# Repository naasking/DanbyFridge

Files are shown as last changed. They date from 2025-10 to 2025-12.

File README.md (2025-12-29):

# Danby Fridge Microcontroller Project

I upcycled an old Danby Fridge, replacing the broken thermostat with an ESP32-C3,
a thermistor for temperature monitoring, and a relay to control the compressor.

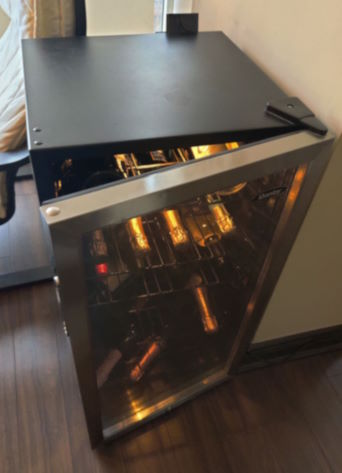
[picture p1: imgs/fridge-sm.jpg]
Danby Fridge
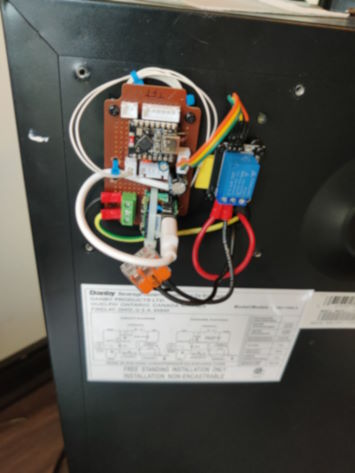
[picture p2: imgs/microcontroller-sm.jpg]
Microcontroller
 

This was also an experiment in AI programming, as the initial skeleton and various
refinements were managed using VS Code + Cline and the gpt-5-mini model, along with
some reviews using Copilot GPT-5.

# User Interface

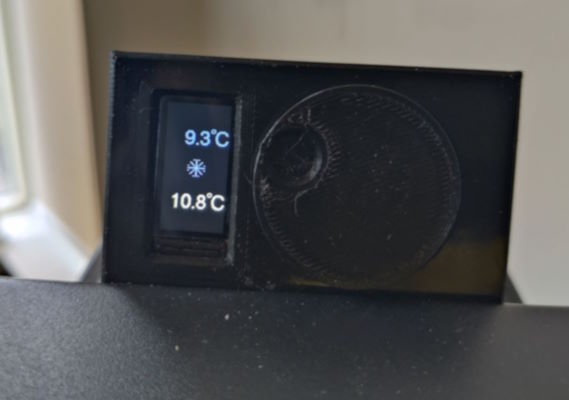
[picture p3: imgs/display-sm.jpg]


Use the dial to set the target temperature, shown in blue at the top. The temperature
at the bottom is the current reading from the thermistor. Press and hold the dial
to switch between Fahrenheit and Celsius.

The snowflake will render when the compressor is actively running, although you can
typically hear it anyway.

# Features

 * Switching between Celsius and Fahrenheit
 * Hysterisis around target temperature
 * Compressor minimum off time to increase longevity of the PTC starter
 * Ratiometric averaging of ADC readings to factor out supply voltage fluctiations
 * Moving averages and dead times to handle ESP32 ADC inaccuracies
 * Periodic state saving only when changes occurred to save on writes

# Design Notes and the AI experience

Using AI for programming can be simultaneously frustrating and humbling. It does a reasonably
good job at following instructions and the code quality is decent, but sometimes we can fall
into rabbit holes without end.

Getting the RMT code working turned out to be futile, but it was never clear whether this was
an issue with the code or the sensor, so I eventually abandoned it for a simple thermistor. I
later discovered a library that does the RMT so maybe I'll try that some day.

There were a few humblind situations where the AI told me of specific issues with
a piece of code, and I thought I had ruled them out, but I'm sometimes not as clever and thorough
as I think.

The `async.h` and `rotary.h` are reusable, standalone headers from my [embedded](https://github.com/naasking/embedded)
repository. They simplified the code a lot, and I was able to easily tell GPT-5 to rewrite
some of the code using these headers. It also suggested a few refinements to the headers
which then made it upstream. Neat.

# Microcontroller Circuit

This is a rough schematic of the controller portion:

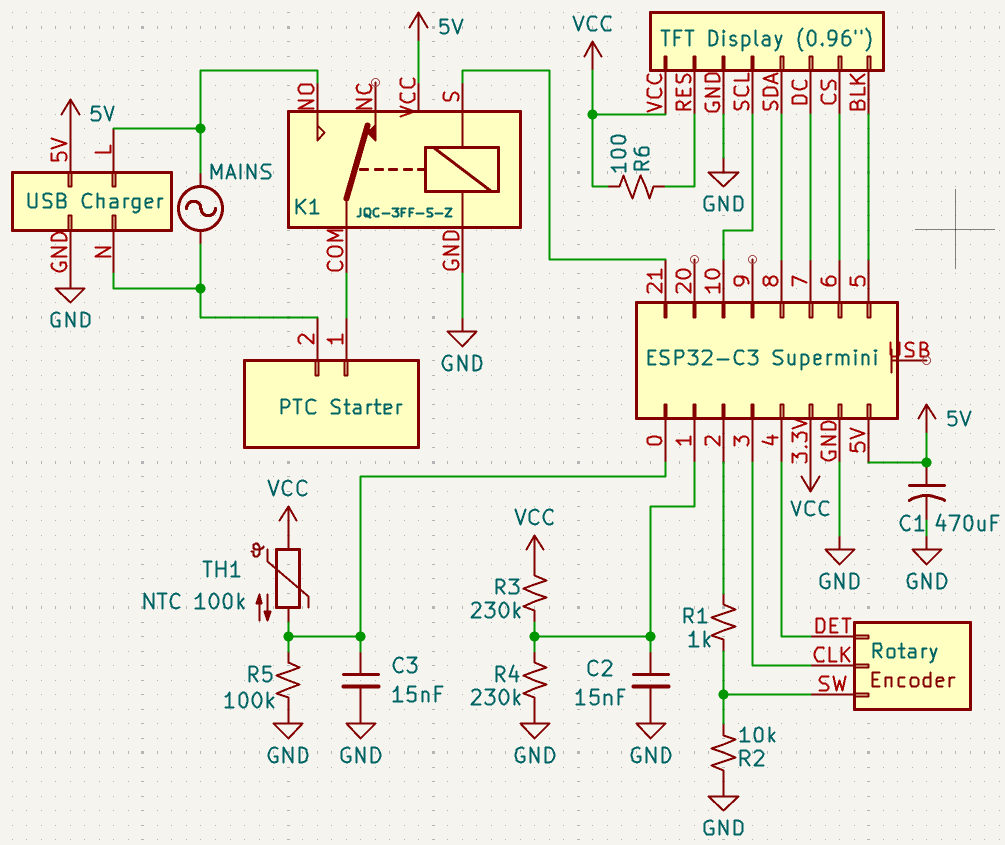
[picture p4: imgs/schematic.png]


It's just missing the small snubber circuit across the relay's AC pins.

# Future Work

## Microcontroller Sleep

I had started with the intention of putting the microcontroller into low power mode
and only powering it up to take measurements every 5 seconds or so. However, I ran into
many difficulties getting RMT to work with the DHT22 sensor I initially started with,
so I disabled a lot of this functionality to try to narrow down the issues I was having
and never got around to adding this back.

## Refactoring

There are a lot of static variables, which limits how you can reuse this code for
different types of fridges. For instance, dual zone wine fridges require multiple
thermistors and multiple relays, which isn't easy with the current code.

All of the static variables should be refactored into structs and initialized in
static arrays whose sizes are set by compile-time constants. This would let the
code scale.

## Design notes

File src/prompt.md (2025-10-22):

Write an Arduino program with the following requirements:

1. It periodically takes temperature readings from a DHT22 sensor.
2. Let's a user modify the target temperature via a HW-040 rotary encoder whose rotation is tracked by an interrupt service routine.
3. Each click of the rotary encoder should correspond to 0.1 degrees C.
4. It displays the current temperature and target temperatures on an ST7735 display, 160x80 resolution.
5. Checks the target and current temperature periodically, and activates a relay when they differ until the current temperature matches the target.
6. It goes into low power mode if no user activity detected for some time.
7. All operations should be non-blocking so the display and rotary encoder counting is responsive.

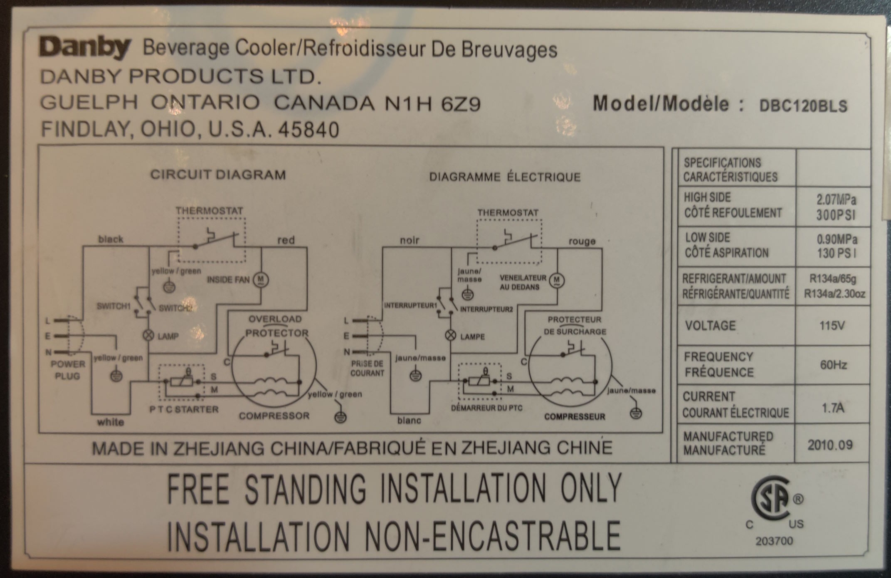
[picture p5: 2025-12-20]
imgs/original circuit.jpg

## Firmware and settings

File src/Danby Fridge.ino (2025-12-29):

#include <Adafruit_ST7735.h>
#include <Fonts/FreeSans12pt7b.h>
#include <SPI.h>                 // ESP32 core SPI
#include <Preferences.h>         // for saving data
#include "rotary.h"
#include <esp_sleep.h>
#include <esp_pm.h>
#include "async.h"

// Preferences instance for non-volatile storage on ESP32
static Preferences prefs;

// === ESP32-C3 Super mini Pin Mapping ===
#define THERM_PIN       0  // Safe -- connected to thermistor
#define RELAY_PIN       21 // Safe -- connected to KY-019 relay module
#define VREF_PIN        1  // Safe -- connected to voltage reference to correct for voltage dips

// Rotary encoder -- grouped on the right side
#define ROTARY_SW       2  // Strapping: should default high
#define ROTARY_CLK      3  // Safe
#define ROTARY_DT       4  // Safe

// TFT SPI -- grouped on the left side
#define TFT_DC          7   // Safe
#define BACKLIGHT_PIN   5   // Safe
#define TFT_CS          6   // Safe
#define TFT_MOSI        8   // SDA-Strapping if GPIO2 is low
#define TFT_SCK         10  // SCL-Safe
#define TFT_MISO       -1   // Not used

// === Notes ===
// - All pins are 3.3V only (no 5V tolerance).

// ADC config
// measured 2.4V on a 3.3V rail as the reference
#define VREF_K          2.41f/3.3f
#define SAMPLES_TOTAL   64
#define SAMPLE_DELAY_MS 10

// Thermistor constants -- use a 100K NTC 3950
// #define R_FIXED 94200.0f    // ~100kΩ reference resistor
// #define R0      125000.0f   // 100kΩ at 25 °C
#define R_FIXED 100000.0f    // ~100kΩ reference resistor
#define R0      100000.0f   // 100kΩ at 25 °C
#define BETA    3950.0f
#define T0      298.15f     // 25 °C in Kelvin

// EMA smoothing factor
#define EMA_ALPHA 0.1f   // adjust between 0.05–0.2 depending on smoothness

#define DISPLAY_UPDATE_INTERVAL 200
#define CONTROL_INTERVAL 10000
#define HYSTERESIS_TENTHS 5      // 0.5°C hysteresis
#define ENCODER_STEP_TENTHS 1    // 0.1°C per encoder step
#define ENCODER_PULSES_PER_STEP 2 // quadrature pulses per mechanical detent (tune if needed)
#define BUTTON_DEBOUNCE_MS 50
#define LONG_PRESS_MS 1000 // ms for long press to toggle units

/* Persistence (Preferences) */
#define SAVE_INTERVAL_MS 5000    // minimum interval between non-volatile writes

// Power management
#define WDT_SLEEP_S 8            // WDT sleep interval in seconds (LowPower SLEEP_8S)
#define CONTROL_INTERVAL_S 10    // control interval in seconds (approximately)
#define DISPLAY_ON_AFTER_WAKE_MS 10000 // keep display on for some time after wake for user feedback
#define COMPRESSOR_MIN_OFF_MS (4UL * 60UL * 1000UL) // 4 minutes minimum off time for compressor starter
#define THERM_START_DELAY 10000

#define _println(text)
#define _printf(fmt, arg0)
//#define _println(text) if (Serial && Serial.isConnected()) Serial._println(text)
//#define _printf(fmt, arg0) if (Serial && Serial.isConnected()) Serial.printf(fmt, arg0)

// RST tied HIGH on module; pass -1 to disable software reset
Adafruit_ST7735 tft = Adafruit_ST7735(TFT_CS, TFT_DC, -1);

// Thermistor async function state
typedef struct {
    async_state;                // the async state
    int sampleCount;            // the number of samples taken
    uint32_t temp;              // accumulated temperature reading
    unsigned long lastSampleMs; // last time a sample was taken
    bool expMovingAvg;          // smoothing is enabled
    float vRef;                 // voltage divider reference
} ThermistorState;

ThermistorState thermState;

// Internal state stored in tenths of °C to avoid non-atomic float access
volatile int16_t targetTenthsC = 250; // tenths of a degree C = 25.0°C

// Quadrature decoder state (4-bit history) and pulse accumulator.
// ISR calls rotary_step() and increments encoderPulseCount.
volatile uint8_t rot_state = 0;
volatile int16_t encoderPulseCount = 0;
 
// Persistence helpers
unsigned long lastSaveMs = 0;

// Compressor/relay safety
bool relayOn = false;
unsigned long lastRelayOffMs = 0;

bool displayCelsius = true;
unsigned long displayOnMs = 0;
unsigned long wdtWakeCount = 0;
float lastValidTempC = NAN;
bool lastButtonState = HIGH;
unsigned long lastButtonMs = 0;
unsigned long pressStartMs = 0;

/// @brief Flag indicating that the target temperature has changed.
/// @remarks Must be a global because changes could happen before the last save window elapses
bool targetDirty = false;
bool unitsDirty = false; // true when the units selection needs persisting

// fixed width text bounds
uint16_t textWidth, textHeight;

void IRAM_ATTR encoderISR() {
  // Minimal ISR: use rotary_step_s16 to update encoderPulseCount directly.
  // rotary_step_s16 expects (count, state, rotb, rota).
  // Read DT (rotb) first, then CLK (rota), and pass in that order to avoid swapped inputs.
  uint8_t a = digitalRead(ROTARY_DT);  // rota (LSB)
  uint8_t b = digitalRead(ROTARY_CLK); // rotb (MSB)
  rotary_step_s16(&encoderPulseCount, &rot_state, b, a);
}

// Wake-only ISR for the rotary button: intentionally empty so its only effect
// is to wake the MCU from sleep. Debounce and button handling remain in loop().
void IRAM_ATTR wakeISR() {
  // no-op: wake-only
}

void setup() {
  // set this LOW immediately so the compressor doesn't immediately turn on
  pinMode(RELAY_PIN, OUTPUT);
  digitalWrite(RELAY_PIN, LOW);

  //Serial.begin(115200, SERIAL_8N1, -1);
  Serial.begin(115200);
  Serial.setTxTimeoutMs(0);
  //delay(3000);
  _println("Program started...");

  // Initialize SPI with explicit pins for ESP32-C3
  SPI.begin(TFT_SCK, TFT_MISO, TFT_MOSI, TFT_CS);

  // Ensure control pins are configured and stable before calling library init.
  pinMode(TFT_CS, OUTPUT);
  pinMode(TFT_DC, OUTPUT);

  // Initialize SPI with a slower clock speed so it's more stable, otherwise
  // the scren sometimes blanks out when receiving many rotary pulses.
  SPI.beginTransaction(SPISettings(4000000, MSBFIRST, SPI_MODE0));
  digitalWrite(TFT_CS, HIGH);
  digitalWrite(TFT_DC, HIGH);
  SPI.endTransaction();

  delay(10); // allow peripheral to settle

  // Call library init (use MINI160x80 PLUGIN for this module)
  tft.initR(INITR_MINI160x80_PLUGIN);
  tft.setFont(&FreeSans12pt7b);
  {
    int16_t x, y;
    char text[] = "-CC.CCC";
    tft.getTextBounds(text, 0, 100, &x, &y, &textWidth, &textHeight);
  }
  tft.setTextSize(1);
  tft.setRotation(0);
  tft.enableDisplay(true);
  tft.fillScreen(ST7735_BLACK);

  pinMode(THERM_PIN, INPUT);
  pinMode(VREF_PIN, INPUT);
  pinMode(ROTARY_CLK, INPUT_PULLUP);
  pinMode(ROTARY_DT, INPUT_PULLUP);
  pinMode(ROTARY_SW, INPUT_PULLUP);

  // Backlight control pin (module BLK has onboard transistor)
  pinMode(BACKLIGHT_PIN, OUTPUT);
  digitalWrite(BACKLIGHT_PIN, HIGH);

  unsigned long now = millis();
  displayOnMs = now + DISPLAY_ON_AFTER_WAKE_MS;

  attachInterrupt(digitalPinToInterrupt(ROTARY_CLK), encoderISR, CHANGE);
  // Also attach to DT so the ISR runs on changes of either channel (better capture on fast/cheap encoders)
  attachInterrupt(digitalPinToInterrupt(ROTARY_DT), encoderISR, CHANGE);
  // Wake-only interrupt for rotary pushbutton (FALLING edge). ISR does nothing
  // beyond waking the MCU; actual button processing is done in the loop.
  attachInterrupt(digitalPinToInterrupt(ROTARY_SW), wakeISR, FALLING);

  // initialize relay OFF (assumes active HIGH; invert logic if needed)
  //FIXME: should maybe check if relay is already on and needs to be?
  digitalWrite(RELAY_PIN, LOW);

  // Load persisted target temperature (tenths of °C). Validate range, otherwise set to current measured temp if available.
  prefs.begin("fridge", false);

  // Try to load saved target
  int16_t saved = prefs.getShort("targetC", INT16_MIN);
  targetTenthsC = saved >= -400 && saved <= 500
    ? saved
    : 250;  // default 25.0C

  // Load persisted units selection (true = Celsius). Default to Celsius if missing.
  displayCelsius = prefs.getBool("unitsC", true);

  // keep Preferences open for the lifetime of the program (do not end here)
  // prefs.end(); // removed to keep prefs active

  // initialize save timestamp to avoid immediate write
  lastSaveMs = now;

  // initialize the thermistor task
  async_init(&thermState);
  thermState.expMovingAvg = false;

  // let system settle for THERM_START_DELAY before reading
  thermState.lastSampleMs = now + THERM_START_DELAY;

  // ensure display shows current values at startup
  updateDisplay(lastValidTempC, targetTenthsC);
}

void show(float temp, int16_t x, int16_t y, uint16_t color) {
  // bounds calculation is slightly off
  tft.setTextColor(color);
  tft.fillRect(x, y - textHeight, textWidth + 20, textHeight + 1, ST77XX_BLACK);
  if (isnan(temp)) {
    // error code should print out 7 chars to match expected length
    tft.setCursor(x, y);
    tft.printf(" - - - - - ");
  } else {
    char buf[16];
    char symbol = displayCelsius ? 'C' : 'F';
    if (!displayCelsius) {
      temp = temp * 9.0 / 5.0 + 32.0;
    }
    // numeric field: width 5 (space/sign + up to 2 digits + '.' + 1 decimal) + " C" = 7 chars
    snprintf(buf, sizeof(buf), "%5.1f %c", temp, symbol);
    // right-align the text
    int16_t x1, y1;
    uint16_t w, h;
    tft.getTextBounds(buf, x, y, &x1, &y1, &w, &h);
    tft.setCursor(78 - w, y);
    tft.print(buf);
    tft.drawCircle(x + textWidth - 4, y - textHeight / 2 + 6, 2, color);
  }
}

void updateDisplay(float currentC, int16_t targetTenths) {
  // Full-screen redraw but use color to distinguish current (white) and target (light blue).
  //_println("updating display...");

  // Target temperature (right) in light blue - also fixed-width
  uint16_t lightBlue = tft.color565(120, 120, 255); // light blue (RGB: 120,120,255)
  float tgtC = targetTenths / 10.0;
  show(tgtC, 0, 50, lightBlue);

  // Current temperature (left) - print fixed-width numeric + unit to avoid residual chars
  show(currentC, 0, 130, ST77XX_WHITE);

  // Compressor running indicator (snowflake) between the values
  // Draw a simple snowflake icon centered at (40, 80)
  int cx = 40, cy = 80, size = 10;
  //tft.fillRect(0, cy - size - 1, 80, size + 1, ST77XX_RED);
  tft.fillRect(0, cy - size, 80, 2*size, ST77XX_BLACK);
  if (relayOn) {
    uint16_t color = lightBlue;
    tft.drawPixel(cx, cy, color);

    // main arms (horizontal & vertical)
    tft.drawLine(cx - size, cy, cx + size, cy, color); // horizontal
    tft.drawLine(cx, cy - size, cx, cy + size, color); // vertical

    // diagonals (scaled to ~70% of size for aesthetics)
    int diag = size * 0.7;
    tft.drawLine(cx - diag, cy - diag, cx + diag, cy + diag, color);
    tft.drawLine(cx - diag, cy + diag, cx + diag, cy - diag, color);

    // small branches: one pixel offset perpendicular to each arm end
    // Horizontal arms
    int bsize = size / 3;
    tft.drawPixel(cx - size, cy - bsize, color);
    tft.drawPixel(cx - size, cy + bsize, color);
    tft.drawPixel(cx + size, cy - bsize, color);
    tft.drawPixel(cx + size, cy + bsize, color);

    // Vertical arms
    tft.drawPixel(cx - bsize, cy - size, color);
    tft.drawPixel(cx + bsize, cy - size, color);
    tft.drawPixel(cx - bsize, cy + size, color);
    tft.drawPixel(cx + bsize, cy + size, color);
  } else {
    // If compressor off, optionally draw a faint outline or nothing. We'll draw nothing.
  }
}

/// @brief  Read the thermistor value.
/// @param s    The thermistor state.
/// @param now  The current time, bound to mills().
/// @return     The async function status.
async readThermistor(ThermistorState *s, unsigned long now, float* temp) {
    async_begin(s);

    s->sampleCount = 0;
    s->temp = 0;
    s->vRef = 0;

    while (s->sampleCount < SAMPLES_TOTAL) {
        // wait between samples for SAMPLE_DELAY_MS
        // also wait at boot for THERM_START_DELAY to start taking measurements
        // to let the system settle
        await(now - s->lastSampleMs < THERM_START_DELAY
           && now - s->lastSampleMs >= SAMPLE_DELAY_MS);
        s->lastSampleMs = now;

        // Read thermistor node
        (void)analogRead(THERM_PIN);   // throw-away after mux switch
        delayMicroseconds(300);
        s->temp += analogRead(THERM_PIN);
        
        // Read 3.3V sense node
        (void)analogRead(VREF_PIN);    // throw-away after mux switch
        delayMicroseconds(300);
        s->vRef += analogRead(VREF_PIN);
        s->sampleCount++;
    }

    // Compute ratiometric average ADC value using a voltage reference on another ADC pin
    {
      float vTemp = (float)s->temp / SAMPLES_TOTAL;
      float vRef = (float)s->vRef / SAMPLES_TOTAL;

      // Compute thermistor resistance
      float rTherm = R_FIXED * (vRef / (vTemp * VREF_K) - 1.0f);

      // Beta equation
      float invT = (1.0f / T0) + (1.0f / BETA) * logf(rTherm / R0);
      float tempK = 1.0f / invT;
      float tempC = tempK - 273.15f - 1.0f; // +1.0C bias as measured by ice slurry
      _printf("Temp: %f", tempC);
      if (s->expMovingAvg) {
        *temp = EMA_ALPHA * tempC  + (1.0f - EMA_ALPHA) * *temp;
      } else {
        s->expMovingAvg = true;
        *temp = tempC;
      }
    }
    async_end;
}

/// @brief Relay control function
/// @returns True if the comrpessor has changed state, false otherwise.
bool controlTemperature(unsigned long now, float currentC, int16_t targetTenths) {
  // Skip if the reading is invalid or if the relay is off and it was on is before the min cool-off
  if (isnan(currentC) || !relayOn && (now - lastRelayOffMs) < COMPRESSOR_MIN_OFF_MS)
    return false;

  int16_t currentTenths = (int16_t)round(currentC * 10.0);

  // Need to turn ON when current is above target plus hysteresis.
  if (!relayOn && currentTenths >= (targetTenths + HYSTERESIS_TENTHS)) {
    // Only allow starting compressor if it is currently off and the minimum off time has elapsed.
    digitalWrite(RELAY_PIN, HIGH);
    relayOn = true;
    return true;
  } else if (relayOn && currentTenths <= (targetTenths - HYSTERESIS_TENTHS)) {
    // Need to turn OFF when current is below target minus hysteresis.
    digitalWrite(RELAY_PIN, LOW);
    relayOn = false;
    lastRelayOffMs = now;
    return true;
  }
  return false;
}

void loop() {
  bool displayDirty = false;
  unsigned long now = millis();
  int16_t pulses = 0;

  // Consume encoder pulses produced by the quadrature ISR and convert pulses -> steps
  {
    noInterrupts();
    pulses = encoderPulseCount;
    encoderPulseCount = 0;
    interrupts();

    if (pulses != 0) {
      static int16_t remainder = 0;
      remainder += pulses;
      int16_t steps = remainder / ENCODER_PULSES_PER_STEP;
      remainder = remainder % ENCODER_PULSES_PER_STEP;

      if (steps != 0) {
        int16_t newTarget = targetTenthsC + (int16_t)(steps * ENCODER_STEP_TENTHS);
        if (newTarget < -100) newTarget = -100;
        if (newTarget > 500)  newTarget = 500;
        if (newTarget != targetTenthsC) {
          targetTenthsC = newTarget;
          targetDirty = true;
          displayDirty = true;
        }
      }
    }
  }

  // button press to wake board from sleep and turn on screen
  // long-press to switch temperature units
  bool sw = digitalRead(ROTARY_SW);
  if (sw == LOW) {
    if (lastButtonState == HIGH && (now - lastButtonMs) > BUTTON_DEBOUNCE_MS) {
      // Debounced button press
      pressStartMs = now;
      lastButtonMs = now;
      displayDirty = true;
    }
    if ((now - pressStartMs) >= LONG_PRESS_MS) {
      // Long press: toggle units
      displayCelsius = !displayCelsius;
      unitsDirty = true;            // mark units changed so we persist it
      pressStartMs = now; // reset the hold period
      displayDirty = true;
    }
  }
  if (sw == HIGH && lastButtonState == LOW && (now - lastButtonMs) > BUTTON_DEBOUNCE_MS) {
    // Button released
    lastButtonMs = now;
  }
  lastButtonState = sw;
  
  // Keep display on for a short period after any updates for user feedback
  // This MUST be a <= comparison as two subsequent iterations might have the same `now` value.
  // While pulses are being registered, this keeps pushing `displayOnMs` forwards and the subsequent
  // loop iterations pull the pin LOW, eventually pushing it HIGH once no pulses are recorded and
  // `now` advances slightly.  This ends up looking like a PWM signal and the screen noticeably
  // dims as a result.
  bool displayOn = (displayOnMs - now) <= (unsigned long)DISPLAY_ON_AFTER_WAKE_MS;
  digitalWrite(BACKLIGHT_PIN, displayOn ? HIGH : LOW);
  
  //  Put MCU to low-power sleep if idle: wake sources are external INT (encoder/button) and timer (approx WDT)
  //  Only sleep if no recent activity and display not required.
  bool idle = (pulses == 0) && !targetDirty && !displayDirty;
  if (!idle) {
    displayOnMs = now + DISPLAY_ON_AFTER_WAKE_MS;
  } else if (!displayOn) {
    // // Configure timer wake for approximately WDT_SLEEP_S seconds (esp_light_sleep)
    // esp_sleep_enable_timer_wakeup((uint64_t)WDT_SLEEP_S * 1000000ULL);
    // // Enter light sleep; external interrupts attached with attachInterrupt() will also wake the chip
    // esp_light_sleep_start();
    // Woke up (either via timer or external INT)
    // wdtWakeCount++;
    // keep display on briefly after wake for feedback
    // displayOnMs = now + DISPLAY_ON_AFTER_WAKE_MS;
  }

  // measure the current temperature
  float t = lastValidTempC;
  if (readThermistor(&thermState, now, &t) == ASYNC_DONE) {
    displayDirty = isnan(lastValidTempC) || abs(t - lastValidTempC) > 0.1f;
    lastValidTempC = t;
    async_init(&thermState);
  }
  
  // Persist target temperature occasionally (rate-limited to SAVE_INTERVAL_MS)
  if ((targetDirty || unitsDirty) && (now - lastSaveMs >= SAVE_INTERVAL_MS)) {
    // Local copies to avoid races with ISRs/other logic
    int16_t toSave = targetTenthsC;
    bool unitsToSave = displayCelsius;
    _println("Save settings");
    // Preferences is already opened in setup and kept open; just write the values
    prefs.putShort("targetC", toSave);
    prefs.putBool("unitsC", unitsToSave);
    lastSaveMs = now;
    targetDirty = false;   // reset dirty state
    unitsDirty = false;
  }
  
  // Relay control based on temperature -- it should monitor temperature regardless
  // of whether something has changed, it should only depend on the amount of time
  // the relay has been off. Mark the display as dirty if the relay changes state.
  displayDirty |= controlTemperature(now, lastValidTempC, targetTenthsC);

  // Single display update point: update once per loop if any condition requested it.
  if (displayDirty) {
    updateDisplay(lastValidTempC, targetTenthsC);
  }
}

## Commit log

2025-10-15 rewritten to handle multiple timing and safety issues
    [Danby Fridge.ino]
2025-10-15 use rotary.h API for handling rotary encoder
2025-10-15 added more options to handle the counting inside rotary.h save the target temperature to EEPROM
2025-10-15 first start initializes target from current ambient temperature reading
2025-10-16 implement low power mode that wakes from interrupts and watchdog to handle any changes
2025-10-18 changed to long-press for switching units, quick press just wakes the screen
2025-10-18 compressor needs to stay off for 3-5 mins for the PTC to cool down render current and target temps in different colours render a snowflake when the compressor is on
2025-10-18 added pin redefinitions for ESP32-C3 mini
2025-10-20 switch board to the ESP32-C3 supermini
2025-10-21 switch to non-blocking DHT reading
2025-10-21 use correct display module don't uninstall driver for each read
    [Danby Fridge.ino]
2025-10-22 documented that GPIO0 is NOT a strapping pin on this board
2025-10-22 removed remaining references to Arduino board
2025-10-22 replace vector with stack arrays
    [Danby Fridge.ino]
2025-10-22 fixed pin mappings based on my ESP32-C3 super mini board TFT_RST is optional tie it high and use that GPIO for the backlight
    [Danby Fridge.ino]
2025-10-23 remapped pins to keep devices all on one side and avoid the internal flash pins added some debugging statements
    [Danby Fridge.ino]
2025-10-23 swap pins so push button can be used to boot into alternate mode
    [Danby Fridge.ino]
2025-10-24 removed SPI transactions that were locking up the device
2025-10-24 get display and rotary encoder to work more reliably
2025-10-25 only update the display once at the end of loop() if an update is needed run SPI at a lower clock speed for stability run an ISR on change for both rotary pins for more resolution temperatures now us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
    [Danby Fridge.ino]
2025-10-25 moved rotary encoder off of the strapping GPIO9 lowered SPI frequency further
2025-10-25 use a sans serif font right-align the temperatures display display the degrees symbol use a vertically oriented display for larger text
2025-10-25 button behaviour fixed
2025-10-26 started testing RMT with explicit error conditions displayed on screen current time should be passed in as a parameter rather than using millis()
    --HG--
    branch : rmt
    [Danby Fridge.ino]
2025-10-27 separated init status from runtime status and added esp_err_t to display any RMT errors for debugging purposes send start pulse before trying to read
    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
    [Danby Fridge.ino]
2025-10-27 abandon DHT22 and switch to thermistor temperature measurement
    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
2025-10-28 working thermistor design
2025-10-28 enabled the temperature control loop properly clear the snowflake when the relay turns off
2025-10-30 use a ratiometric temperature measure to compensate for voltage sag
    [Danby Fridge.ino]
2025-10-30 move targetDirty to global state so it's properly saved delay the start of temperature readings to let the system settle
2025-10-30 saved and restore temperature units
2025-11-08 reassign a few pins for wiring convenience to a header renamed variable displayOnUntilMs to displayOnMs for clarity
2025-11-17 fixed screen dimming bug specify exact COM port
    [Danby Fridge.ino]
2025-11-21 turn the relay off immediately correct thermistor positive bias mark display dirty when the relay changes added missing files
    [Danby Fridge.ino]
2025-12-20 fixed temperature bias removed unneeded headers
    [Danby Fridge.ino]
2025-12-29 added kicad schematic for the microcontroller
    [Control board.kicad_sch]
2025-12-29 updated README with schematic
2025-12-29 added USB charger to the overall circuit to clarify power feed
    [Control board.kicad_sch]
2025-12-29 moved capacitor to relay power pin
    [Control board.kicad_sch]
2025-12-29 C1 is actually to stabilize ESP32 power for the ADC
    [Control board.kicad_sch]
